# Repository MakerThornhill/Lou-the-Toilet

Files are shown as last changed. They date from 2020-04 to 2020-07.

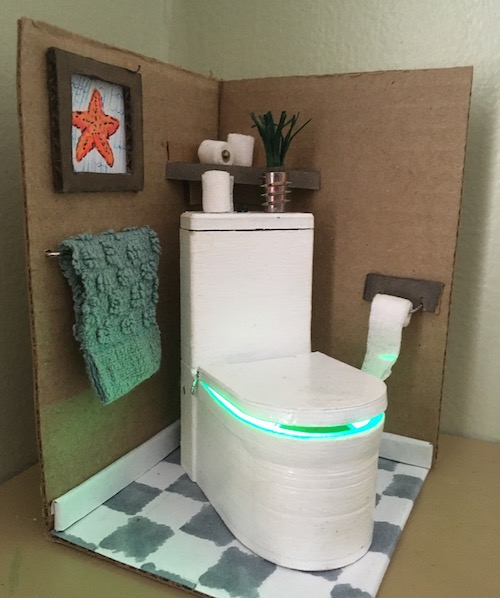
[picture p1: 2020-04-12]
Images/Lou_full-model_500.JPG

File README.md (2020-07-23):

# Lou-the-Toilet
Cute as a button, this lil' internet-connected, miniature toilet model sits on my desk and lets me know when the house's only bathroom is free.

Equipped with a servo, a neopixel, and a ESP32 breakout board, Lou the Toilet glows different colours and raises and lowers its lid to indicate if the bathroom is occupied.

Powered by Arduino and using Adafruit's IO service (https://io.adafruit.com/), Lou uses a separate internet-connected microcontroller, a magnetic door switch, and a light sensor to determine whether the bathroom is free and clear!

More project details: https://hackaday.io/project/170829-lou-the-toilet-indicator

Lou the Toilet - full model

## The Project
**Lou the Toilet** is a 3D printed miniature toilet that uses an [Adafruit ItsyBitsy 32u4 5V](https://www.adafruit.com/product/3677), a miniature servo, and a neopixel to indicate the status of the bathroom with a lifting and closing of it's lid and a coloured glow. An ESP32 breakout board (Adafruit AirLift – ESP32 WiFi Co-Processor) lets Lou connect to the internet and the Adafruit IO service to get updates about the bathroom's availability.

Just provide Lou with 5v and it's good to go, merrily opening and closing its lid all day!

**The Bathroom Occupancy Detector** covers the bathroom side, and is made up of an [Adafruit ItsyBitsy M0](https://www.adafruit.com/product/3727) with an ESP32 add-on (Airlift Bitsy), a magnetic door switch, and a light sensor. Together they monitor the state of the door (open or closed) and the bathroom light (off or on) to determine whether the bathroom is free. 

The bathroom status can be viewed anywhere from the house, using Lou or a private Adafruit IO dashboard.

## The Code
Lou and the Occupancy Dector use Arduino and the [Arduino Adafruit IO library](https://github.com/adafruit/Adafruit_IO_Arduino). Examples of how to use the Adafruit IO and it's libraries can be found in the [Adafruit IO learn guide](https://learn.adafruit.com/welcome-to-adafruit-io).

**Required Libraries:**
- [Arduino Adafruit IO library](https://github.com/adafruit/Adafruit_IO_Arduino).
- [Adafruit NeoPixel](https://github.com/adafruit/Adafruit_NeoPixel) 
- [Adafruit Dotstar](https://github.com/adafruit/Adafruit_DotStar)
- Servo

## 3D Model & Print files
Lou is based on a [GrabCad toilet model](https://grabcad.com/library/gustavsberg-artic-4300-1) by [Jari Ikonen](https://grabcad.com/jari.ikonen-2). I edited the design in Fusion 360 to fit the electronics and house the stop sign when the lid is closed.

Other parts, including the stop sign and case for the Occupancy Detector were designed by me. You can find print files within the 3D_Print_files folder!

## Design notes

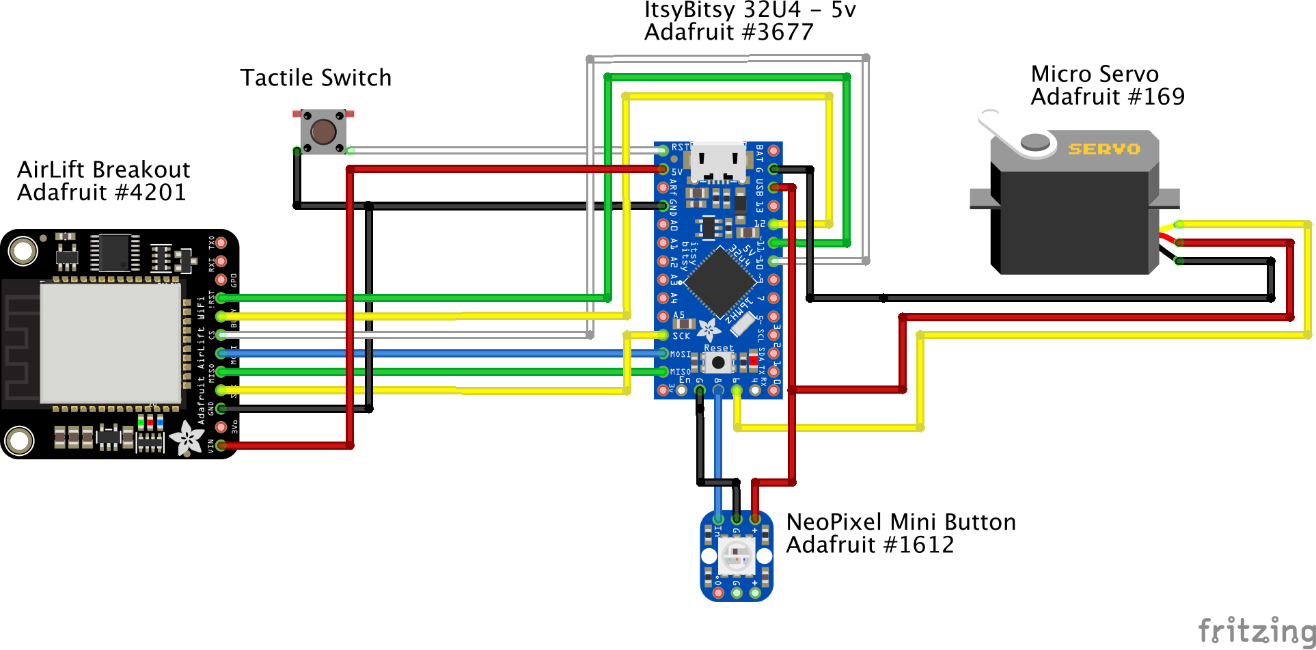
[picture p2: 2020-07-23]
Images/Lou_schematic_v1.2.png

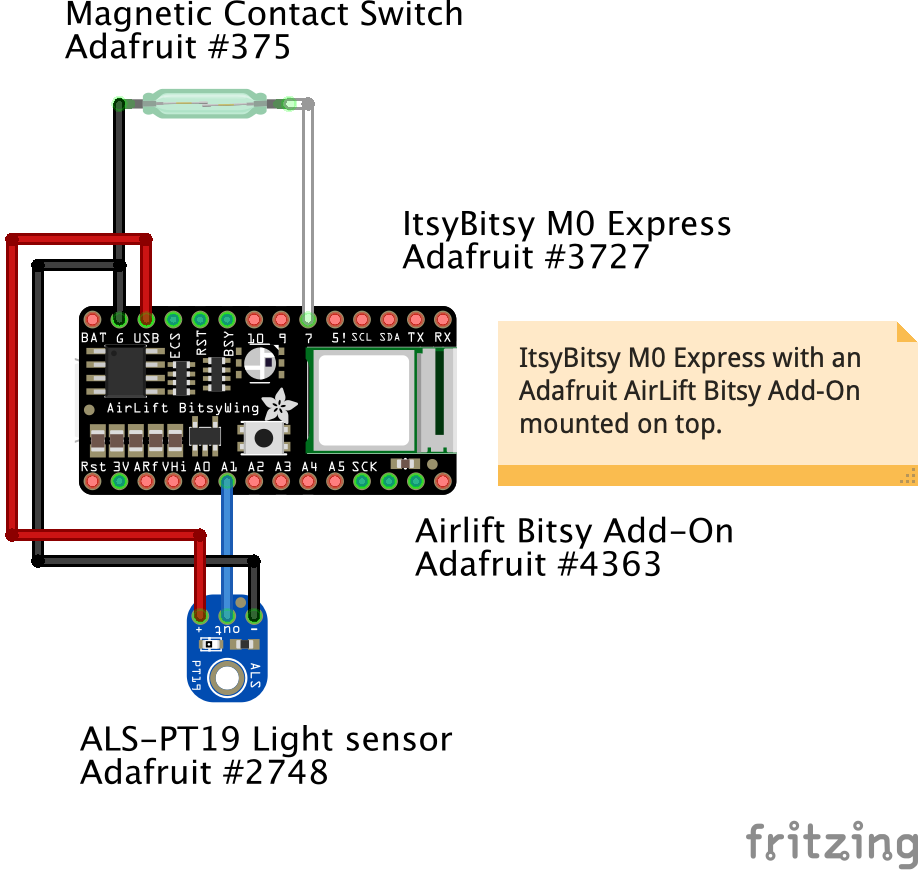
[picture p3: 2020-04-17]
Images/Occupancy_schematic_v1.png

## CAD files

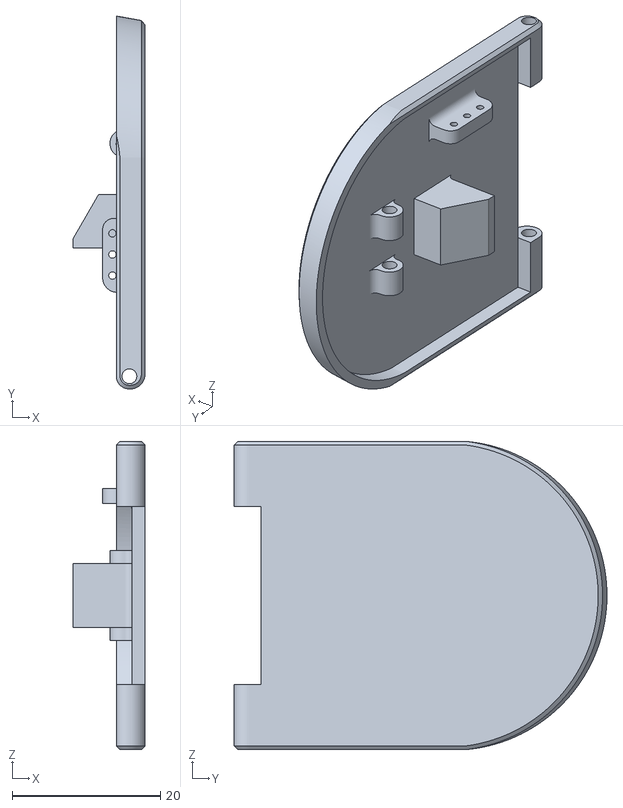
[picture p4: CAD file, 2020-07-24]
3D_Print_files/Lou_seat_lid.stl
9.73 x 50.3 x 41.6

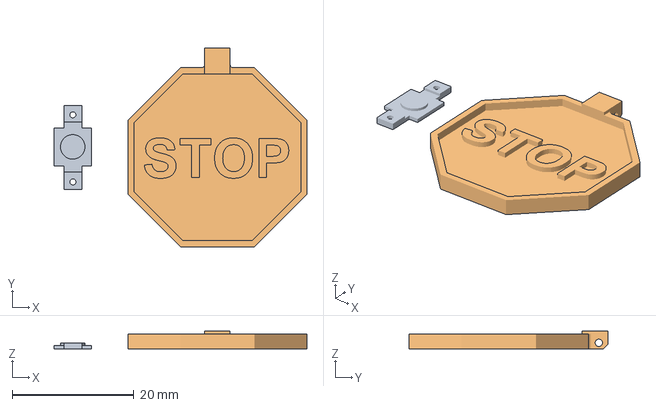
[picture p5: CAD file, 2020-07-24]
3D_Print_files/Stop_sign.3mf
41.6 x 32.6 x 2.95 mm
Button_cover.stl
Stop2.stl

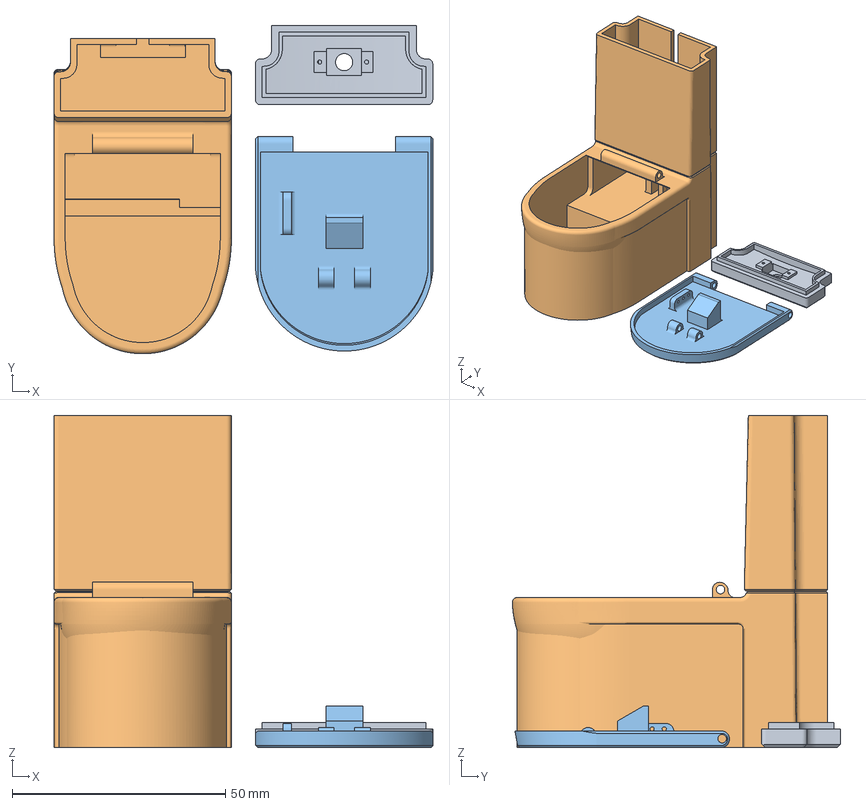
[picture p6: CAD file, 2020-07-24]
3D_Print_files/Lou_combined_group_1.3mf
88.9 x 77.1 x 78.0 mm
Cistern_lid.stl
Lou_body_v2.stl
Lou_seat_lid.stl

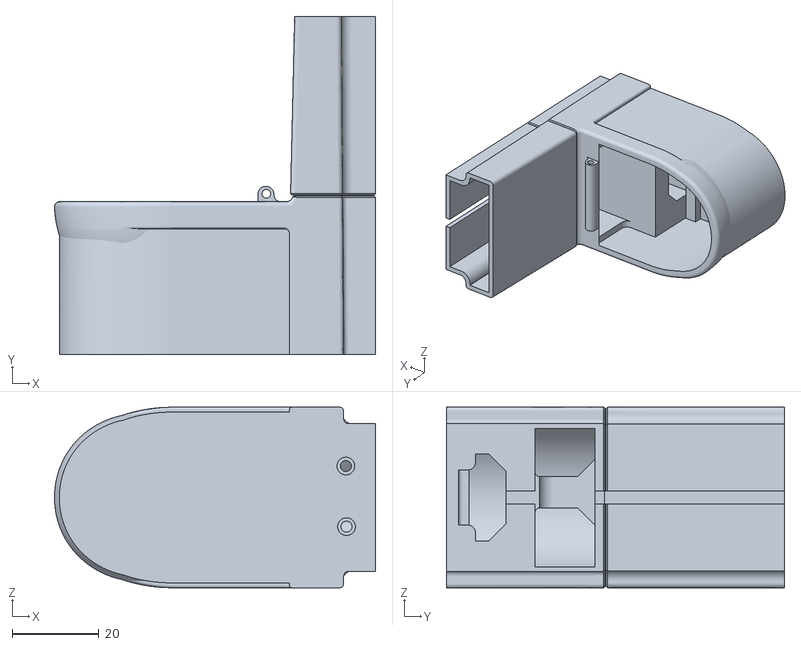
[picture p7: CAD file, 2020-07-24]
3D_Print_files/Lou_body_v2.stl
74.0 x 78.0 x 41.7

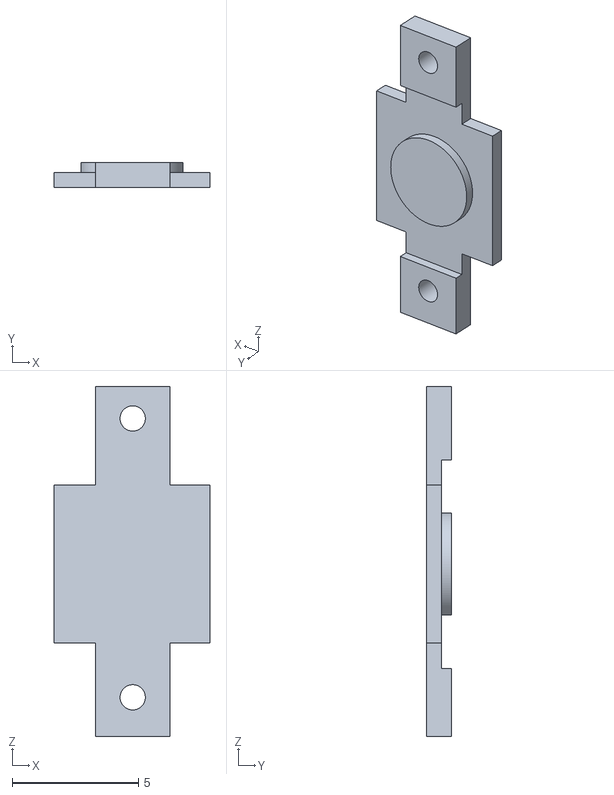
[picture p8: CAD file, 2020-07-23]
3D_Print_files/Button_plate.stl
6.15 x 1.00 x 13.8

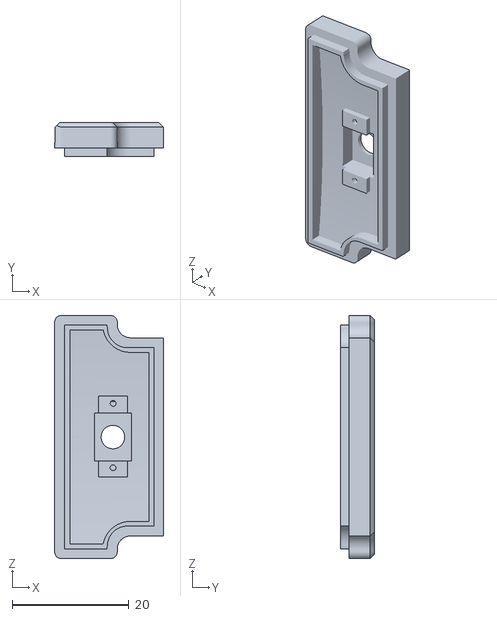
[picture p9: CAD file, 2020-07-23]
3D_Print_files/Lou_cistern_lid.stl
18.6 x 5.90 x 41.6

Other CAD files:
3D_Print_files/Lou_body.stl
3D_Print_files/Stop_sign.stl

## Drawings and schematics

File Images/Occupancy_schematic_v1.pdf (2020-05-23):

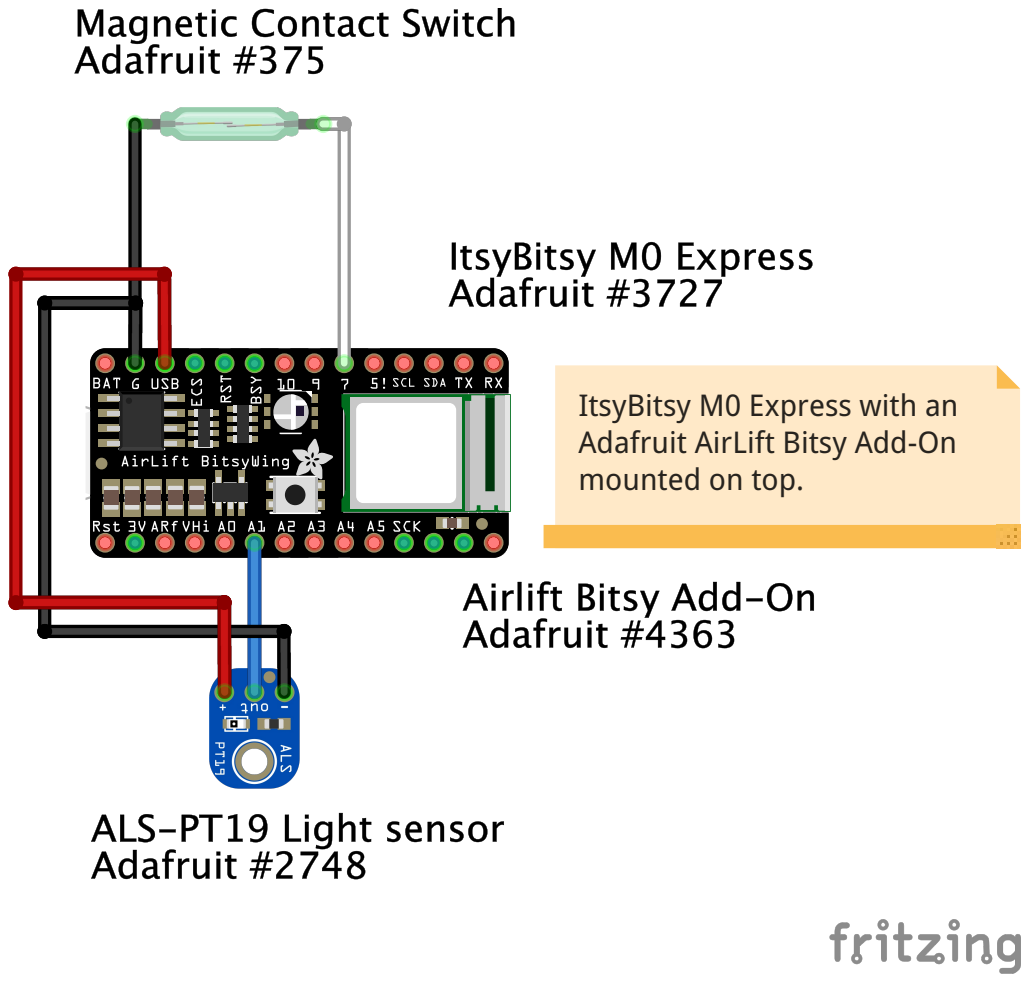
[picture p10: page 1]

ItsyBitsy M0 Express with an
Adafruit AirLift Bitsy Add-On
mounted on top.

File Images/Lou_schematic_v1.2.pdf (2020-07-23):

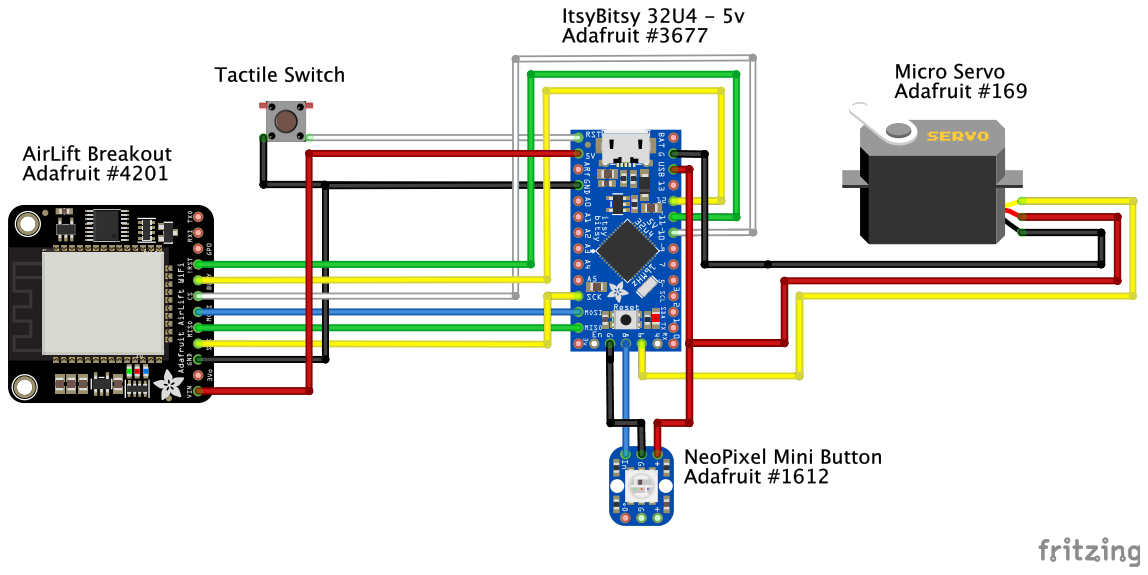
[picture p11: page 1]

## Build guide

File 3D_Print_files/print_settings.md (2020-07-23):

# Print Settings

You'll find printable STLs in the 3D_print_file section. The majority of the parts were printed with the following settings:

| |  |
| --- | --- |
| **Material:** | PLA |
| **Layer Height:**| 0.2 mm|
| **Infill:**| 15% Gyroid|
| **Supports:**| Support enforcer only used in the main Lou body, and only for the area that holds the servo|

The majority of the parts were printed at the same time and should take just over 4 hours to print. 

The stop sign was printed in silver and red, with a colour change to really make the text pop.

I'll be adding a .3mf file to make things easier!

[2020-07-23]: Added a new version of Lou, with a gap in the back to help with wire routing.

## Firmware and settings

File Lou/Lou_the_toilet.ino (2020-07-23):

/*----------------------------------------
    Lou the Toilet -- by Thornhill!
  ----------------------------------------

  Minature toilet with motorised lid and NeoPixel. Connects to Adafruit IO 
  and the Bathroom status feed to indicate whether the bathroom is occupied
  or not. 

  Board:    Adafruit ItsyBitsy 32u4 5v
  Airlift:  Adafruit AirLift – ESP32 WiFi Co-Processor Breakout Board (https://www.adafruit.com/product/4201)

  Other:    RadioShack Digital Micro servo
            NeoPixel Mini Button PCB


************************* Configuration ***********************************

  // edit the config.h tab and enter your Adafruit IO credentials
  // and any additional configuration needed for WiFi, cellular,
  // or ethernet clients.

****************************************************************************/
#include "config.h"
#include <Adafruit_NeoPixel.h>
#include <Servo.h>

//Pins
#define SERVO_PIN     6
#define PIXEL_PIN     8
#define PIXEL_COUNT   1
#define PIXEL_TYPE    NEO_GRB + NEO_KHZ800

//Initial servo position for toilet lid, almost fully upright
byte servo_pos = 10;
byte prev_pos = 10;
byte pos;

Adafruit_NeoPixel pixels = Adafruit_NeoPixel(PIXEL_COUNT, PIXEL_PIN, PIXEL_TYPE);
Servo myservo;

AdafruitIO_Feed *bathroom_status = io.feed("status");

void setup() {
  Serial.begin(115200);

  //Add neopixel
  pixels.begin();
  pixels.clear();
  pixels.show();
  
  //Change to blue to let us know it's ready to connect
  pixels.setPixelColor(0, pixels.Color(0, 0, 150));
  pixels.show();

  //************ Connect to Adafruit IO ************//
  Serial.print("Connecting to Adafruit IO");
  io.connect();

  bathroom_status->onMessage(handleMessage);
  
  // Try to connect
  while (io.status() < AIO_CONNECTED) {
    //A pink-magenta colour lets us know it's having some problems
    pixels.setPixelColor(0, pixels.Color(150, 0, 150));
    pixels.show();
    delay(1000);
    Serial.print("...");
    Serial.print(io.statusText());
    pixels.clear();
    pixels.show();
    delay(1000);
  }

  // We are connected
  Serial.println();
  Serial.println(io.statusText());

  bathroom_status->get();

  //White colour because everything is dandy
  pixels.setPixelColor(0, pixels.Color(150, 150, 150));
  pixels.show();

  //*************************************//

  myservo.attach(SERVO_PIN);
  myservo.write(10);

  pixels.clear();

}

void loop() {
  io.run();
}

void handleMessage(AdafruitIO_Data *data) {

  Serial.print("Received: ");
  Serial.println(data->value());

  
  //Convert received data to an Int
  int toilet_reading = data->toInt();

  switch (toilet_reading) {
    case 0: //Not free
      servo_pos = 50; //Open enough to see the stop sign
      pixels.setPixelColor(0, pixels.Color(255, 0, 1));
      break;
    case 1: //Maybe free
      servo_pos = 70; //Midway
      pixels.setPixelColor(0, pixels.Color(255, 75, 0));
      break;
    case 2://Free!
      servo_pos = 97; //Almost shut... enough for that sweet green glow
      pixels.setPixelColor(0, pixels.Color(0, 255, 0));
      break;
  }

  pixels.show();
  
  //To decrease the servo position (i.e. servo is at 45... but needs to be 0...)
  if (servo_pos < prev_pos) { //  i.e. servo is at 45... but needs to be 0....
    for (pos = prev_pos; pos >= servo_pos; pos -= 1) { 
      myservo.write(pos);
      delay(75);
    }
  }
  //To increase the servo positoon (i.e. servo is at 0... but needs to be 45...)
  else if (servo_pos > prev_pos) { 
    for (pos = prev_pos; pos <= servo_pos; pos += 1) { 
      myservo.write(pos);
      delay(75);
    }
  }
  else {
  }
  prev_pos = servo_pos;

}

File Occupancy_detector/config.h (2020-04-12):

/************************ Adafruit IO Config *******************************/

// visit io.adafruit.com if you need to create an account,
// or if you need your Adafruit IO key.
#define IO_USERNAME  "EXAMPLE"
#define IO_KEY       "EXAMPLE_KEY"      

/******************************* WIFI **************************************/

// the AdafruitIO_WiFi client will work with the following boards:
//   - HUZZAH ESP8266 Breakout -> https://www.adafruit.com/products/2471
//   - Feather HUZZAH ESP8266 -> https://www.adafruit.com/products/2821
//   - Feather HUZZAH ESP32 -> https://www.adafruit.com/product/3405
//   - Feather M0 WiFi -> https://www.adafruit.com/products/3010
//   - Feather WICED -> https://www.adafruit.com/products/3056
//   - Adafruit PyPortal -> https://www.adafruit.com/product/4116
//   - Adafruit Metro M4 Express AirLift Lite ->
//   https://www.adafruit.com/product/4000
//   - Adafruit AirLift Breakout -> https://www.adafruit.com/product/4201
//   - Adafruit AirLift Shield -> https://www.adafruit.com/product/4285
//   - Adafruit AirLift FeatherWing -> https://www.adafruit.com/product/4264

#define WIFI_SSID "EXAMPLE_SSID"
#define WIFI_PASS "EXAMPLE_PASS"

// uncomment the following line if you are using airlift
#define USE_AIRLIFT
#include "AdafruitIO_WiFi.h"

#if defined(USE_AIRLIFT)
  #define SPIWIFI       SPI  // The SPI port
  #define SPIWIFI_SS    13   // Chip select pin
  #define ESP32_RESETN  12   // Reset pin
  #define SPIWIFI_ACK   11   // a.k.a BUSY or READY pin
  #define ESP32_GPIO0   -1
#endif

AdafruitIO_WiFi io(IO_USERNAME, IO_KEY, WIFI_SSID, WIFI_PASS, SPIWIFI_SS,
                   SPIWIFI_ACK, ESP32_RESETN, ESP32_GPIO0, &SPIWIFI);

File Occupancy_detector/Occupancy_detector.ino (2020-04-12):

/*----------------------------------------
    Bathroom Occupancy Detector -- by Thornhill!
  ----------------------------------------

   Bathroom occupancy detector, using a magnetic door switch and a light sensor.
   Pushed to Adafruit IO via an Adafruit ESP32 Airlift board.

   Assumes when door the is open and the light is off, the bathroom is free (which
   is how we roll in this household). When the door is open but the light is on,
   the bathroom might not be free. A closed door always assumes the bathroom is
   occupied.

   Board:     ItsyBitsy M0
   Airlift:   Airlift Bitsy (https://www.adafruit.com/product/4363)

   Sensors:
              Magnetic Door sensor (https://www.adafruit.com/product/375)
              ALS PT19 Light sensor (https://www.adafruit.com/product/2748)


    Based on https://learn.adafruit.com/using-ifttt-with-adafruit-io



  /************************** Configuration ***********************************/

// edit the config.h tab and enter your Adafruit IO credentials
// and any additional configuration needed for WiFi, cellular,
// or ethernet clients.
#include "config.h"
/****************************************************************************/

#include <Adafruit_DotStar.h>

//Pins
#define DOOR_PIN        7
#define LIGHT_PIN       A1
#define DATAPIN         41 //for the ItsyBitsy's onboard Dotstar
#define CLOCKPIN        40 //for the ItsyBitsy's onboard Dotstar

//Settings
#define LIGHT_THRESHOLD 60 //Trigger threshold for light level
#define IO_LOOP_DELAY   5000
#define NUMPIXELS       1 //number of dotstars

#define OPEN    0
#define CLOSED  1
#define ON      1
#define OFF     0

unsigned long lastUpdate = 0;
unsigned long lastStateChange = 0;
unsigned long durationSecs;

byte door_state;
byte light_state;
byte status_num;
String status_string = "***** Standby! *****";

char *lightStates[] = {"Off", "On"};
char *doorStates[] = {"Open", "Closed"};

byte prev_state;
byte current_state;

byte prev_door;
byte current_door;

byte prev_light;
byte current_light;

Adafruit_DotStar dot(NUMPIXELS, DATAPIN, CLOCKPIN, DOTSTAR_BRG);

//The various Adafruit IO feeds we want to publish.
//We definitely need the Status feed, the others are for completeness. 

AdafruitIO_Feed *bathroom_status = io.feed("status");
AdafruitIO_Feed *door = io.feed("toilet-or-not-toilet.door");
AdafruitIO_Feed *light = io.feed("toilet-or-not-toilet.light");
AdafruitIO_Feed *bathroom_status_string = io.feed("toilet-or-not-toilet.status-string");
AdafruitIO_Feed *duration = io.feed("toilet-or-not-toilet.duration");


void setup() {
  Serial.begin(115200);

  //Initialise the dotstar
  dot.begin(); 
  dot.setBrightness(80);
  dot.show();
  
  //Blue colour to show we'r going to connect
  dot.setPixelColor(0, 0, 0, 255);
  dot.show();

  //********* Connect to Adafruit IO **********

  Serial.print("Connecting to Adafruit IO... ");
  io.connect();

  //Wait for connection... and flash a magenta colour
  //if we need to really wait... 
  while (io.status() < AIO_CONNECTED) {
    dot.setPixelColor(0, 0, 150, 150);
    dot.show();
    delay(1000);
    Serial.print("StatusText:");
    Serial.print(io.statusText());
    Serial.println("..");
    dot.clear();
    dot.show();
    delay(1000);
  }

  //Connected!
  Serial.print(io.statusText());
  Serial.println();
  setColor(0, 255, 0);//Green, all good!

  //***********************************

  //Set up pins

  pinMode(DOOR_PIN, INPUT_PULLUP);
  
}

void loop() {
  io.run();

  if (io.status() < AIO_CONNECTED) {
    setColor(255, 0, 0);
    connect_AIO();
  }

  //Check the door switch and light sensor
  sensors();

  //Conditions to determine occupancy based on
  //the sensor states.
  if ((door_state == 1 && light_state == 1) || (door_state == 1 && light_state == 0)) { //Door is closed, light is on/off
    status_num = 0;
    status_string = "Not free!";
  }
  else if ((door_state == 0 && light_state == 1)) {
    //Door is open, light is on..
    status_num = 1;
    status_string = "Maybe not free";
  }
  else if (door_state == 0 && light_state == 0) { //Door is open, light is off
    status_num = 2;
    status_string = "Free!";
  }

  current_state = status_num;

  //Check if enough time has passed and then check if there's been a change in state...
  if (millis() > (lastUpdate + IO_LOOP_DELAY)) {
    setColor(0, 255, 0);//Green, all good!

    if (prev_state != current_state) {
      setColor(0, 0, 255);
      unsigned long durationMillis = millis() - lastStateChange;
      durationSecs = durationMillis / 1000;

      Serial.print(status_string);
      Serial.print(" Last state change: ");
      Serial.print(durationSecs);
      Serial.print("s, ");
      Serial.print(durationMillis);
      Serial.println(" ms");

      //If the bathroom is currently free, then send the duration of
      //when it wasn't free. Otherwise just make the duration 0.
      if (current_state == 2) {
        push_to_AIO(durationSecs);
      }
      else {
        push_to_AIO(0);
      }

      prev_state = current_state;
      lastStateChange = millis();
    }
    lastUpdate = millis();
  }
}

void sensors() {

  //Reading the door sensor
  if (digitalRead(DOOR_PIN) == LOW) {
    door_state = CLOSED;
  }
  else {
    door_state = OPEN;
  }
  current_door = door_state;

  //Set up and read the light sensor
  int level_raw = analogRead(LIGHT_PIN); //Read light value

  if (level_raw > LIGHT_THRESHOLD) {
    light_state = ON; //light is on
  } else {
    light_state = OFF; //light if off
  }

  current_light = light_state;

  if ((prev_door != door_state) || (prev_light != light_state)) {
    Serial.println();
    Serial.print("Door: ");
    Serial.println(doorStates[door_state]);
    Serial.print("Light: ");
    Serial.print(lightStates[light_state]);
    Serial.print(" (raw) = ");
    Serial.print(level_raw);
    Serial.println();
  }
  prev_light = current_light;
  prev_door = current_door;
}

void push_to_AIO(float duration_) {
  bathroom_status->save(status_num);
  bathroom_status_string->save(status_string);
  door->save(door_state);
  light->save(light_state);
  duration->save(duration_);
  io.run();
}

void connect_AIO() {
  Serial.println();
  Serial.print("Reconnecting to Adafruit IO...");
  io.connect();

  // wait for a connection
  while (io.status() < AIO_CONNECTED) {
    Serial.print(".");
    delay(500);
  }

  // we are connected
  Serial.print(io.statusText());
  setColor(255, 255, 255);
  Serial.println();
}

//Function to set the colour on both the dotstar and the airlift's 
//RGB led...
void setColor(int red, int green, int blue)
{
  WiFi.setLEDs(green, red, blue);
  dot.setPixelColor(0, green, red, blue);
  dot.show();
}

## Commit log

2020-04-11 Added the main Arduino files for Lou the Toilet
2020-04-17 Added Fritzing schematics
2020-05-23 Latest schematics
    Forgot to add a reset switch — added with v1.1 of the Lou schematic. Also included PDF versions.
2020-07-23 New schematic
    Swapped some pins around. Changed wire colours & routing.
2020-07-23 Added Lou STLs
    [Button_plate.stl, Lou_body.stl, Lou_body_v2.stl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]
2020-07-24 Add files via upload
    Updated the seat lid to bump out the stop sign more. Also updated main lou body to make a snug fit for the servo.
    Added some .3mf files for people who want the settings and the parts together.
    [Lou_body_v2.stl, Lou_combined_group_1.3mf, Lou_seat_lid.stl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]
